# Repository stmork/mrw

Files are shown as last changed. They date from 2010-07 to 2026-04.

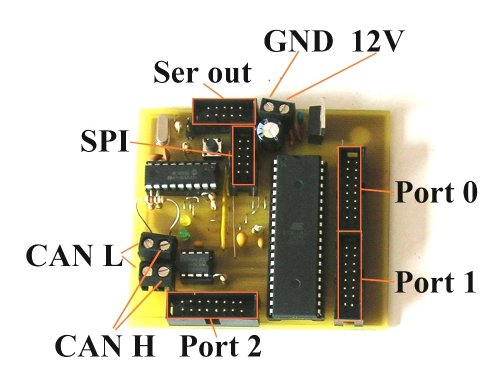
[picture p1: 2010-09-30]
Bilder/Trac/ControllerModul/AnschluesseMC.jpg

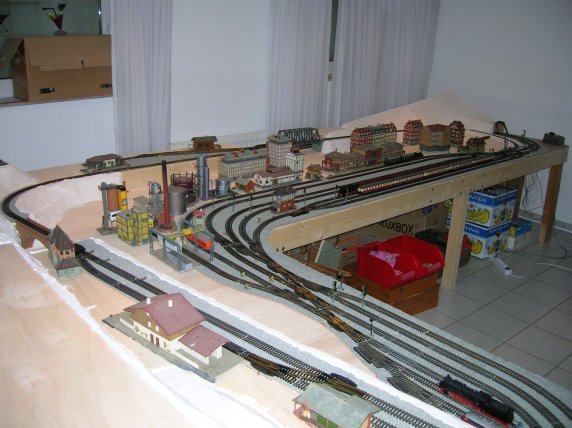
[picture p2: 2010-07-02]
Bilder/Trac/AnlageZwei/dscn4039.jpg

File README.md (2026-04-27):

# Modell(-bau-)basierte Eisenbahnsteuerung

Herzlich Willkommen auf den Informationsseiten der modell(-bau-)basierten
Eisenbahnsteuerung! Auf diesen Seiten wird die Entwicklung einer
eigenständig entwickelten Eisenbahnsteuerung dargestellt. Alle Ergebnisse
können auf diesen Seiten als Open Source (Eclipse Public Licence) eingesehen
werden. Schaut Euch den Quellcode an und nehmt Einblick in die
technischen Hintergründe des CAN-Bus und Microcontroller-Programmierung mit
dem ATmega32. Die ausführliche API bietet weiteres Hintergrundmaterial.
Schauen Sie sich auch die vielen
[Videos auf YouTube](https://www.youtube.com/playlist?list=PL6E0B186E9CC98026) an!

Viel Spaß!!

## Build- und Modellarchitektur

```mermaid
flowchart TB
subgraph Eclipse
 Modelrailway.umlclass -- converts --> Ecore --> GenModel
 GenModel --> Modelleditor-Plugin -- edit --> MRW.modelrailway
 Ecore --> Modelleditor-Plugin
 Ecore --> MRW-Generator --> MRW-Classes
 Xtext --> MRW-Generator
 MRW.modelrailway -- generates --> MRW-Classes -- compiles --> Control-Plugin
 end
 Control-Plugin -- deploys --> Application
 subgraph Eclipse-RPC-Application
 Application -. uses .-> Signal.properties
 Application -. uses .-> Gruppe.properties
 Application -. uses .-> Gleisteile.properties
 end

```

## MRW Firmware
Die Firmware ist in ein eigenes Repository migriert und wird hier nicht mehr
gepflegt.

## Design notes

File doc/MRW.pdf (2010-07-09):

## Modell(-bau-)getriebene Eisenbahnsteuerung

Motivation
Der Bau einer Modelleisenbahnanlage ist nicht nur technisch eine Herausforderung. Viele Kabel müssen über Kopf verlegt werden. Zum Teil ist die Topologie der Anlage so, dass viele Stellen relativ unzugänglich sind. Kann dort Verkabelung reduziert werden, vereinfacht das im erheblichen Maße die Installation. Aus diesem Grunde wurde die Steuerung so konzipiert, dass möglichst viel Verkabelungsaufwand gespart werden soll. Bei einer klassischen Anlage werden alle zu steuernden Bauteile mit dem Stellwerk verbunden. Eine simple Weiche hat drei Anschlüsse. Bei 30 Weichen sind das schon knapp hundert Kabel, die zum Teil über weite Strecken geführt werden müssen. Aus diesem Grund ist die Steuerung der Bauteile möglichst nah anzubringen. Es verbleibt nur noch die Stromversorgung und die Kommunikationsleitungen, die anlagenweit anzubringen sind. Die Steuermodule – im Folgenden CAN-
Knoten | genannt | - | sind | nicht
spezialisiert, das heißt, dass sie über ihre Mehrzweck-IO-Leitungen alle

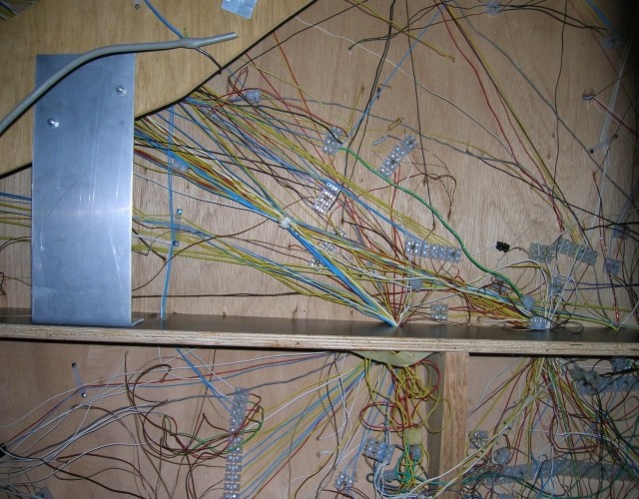
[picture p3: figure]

möglichen Erweiterungen ansteuern können. Die Gerätemodule haben keine Eigenintelligenz und dienen als Schnittstelle und Leistungsverstärker bzw. Schalter zwischen dem CAN-Knoten und dem Bauteil. Die Bauteile der Eisenbahnanlage werden direkt an die Gerätemodule angeschlossen und diese wiederum per Flachbandkabel an die Mehrzweckanschlüsse der CAN-Knoten. Jeder CAN-Knoten hat drei dieser Anschlüsse. Als zusätzliche Anschlussmöglichkeit hat jeder CAN-Knoten einen seriellen Anschluss, mit dem ein spezielles Lichtsignalmodul über ein 10-poliges Flachbandkabel angeschlossen werden kann. Die reine Verkabelung meiner eigenen Anlage mit 29 Weichen, 84 Gleisabschnitten, 45 Signalen gesteuert von 15 CAN-Knoten hat gerade mal fünf volle Tage gedauert.

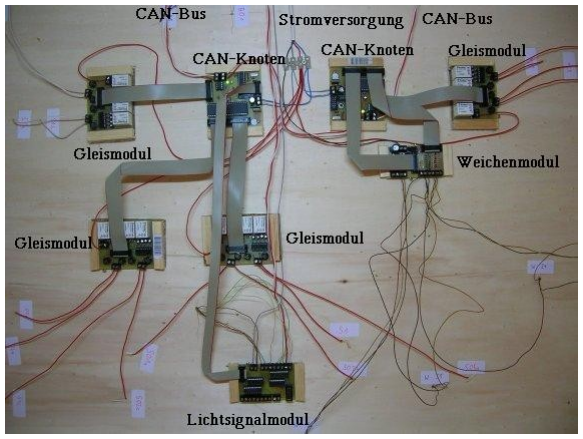
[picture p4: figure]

Als | Bussystem | wurde | CAN
gewählt. Ursprünglich von Bosch
entwickelt, wird es in fast jedem neueren Fahrzeug als Bussystem
verwendet. | Durch | die | raue
Umgebung im Automobil gilt der CAN-Bus als sehr robust und findet immer mehr Verwendung auch in anderen Bereichen, etwa in der
Automatisierungstechnik. | Auf
Grund | der | zwanzigjährigen
Geschichte ist | der CAN-Bus
ausgereift | und | kostengünstig
verfügbar. | Auf | die | in | der
Modellbahnwelt | benutzten
Protokolle wie z.B. DCC wurde bewusst verzichtet. Zum einen ist DCC nur eine Teillösung, weil eine Ansteuerung durch einen Rechner nicht in einer Spezifikation abgedeckt ist. Zum anderen ist die Möglichkeit der Rückmeldung begrenzt. DCC ist ursprünglich unidirektional ausgelegt. Die bidirektionale Nutzung liegt derzeit nur als Empfehlung vor. Des Weiteren haben sich andere Protokolle, die der Rückmeldung dienen etabliert. Insgesamt ist dadurch der Digitalmarkt im Modellbahnumfeld relativ unübersichtlich. Bei der Entwicklung der Steuerung ging es auch nicht darum, eine weitere Steuerung auf den Markt zu bringen und anderen Systemen Konkurrenz zum machen, sondern eine Machbarkeitsstudie für eine modellgetriebene Mikrocontroller-Firmware zu entwickeln. Aus diesem Grund wurde die Steuerung samt Rückmeldungsmöglichkeit als Ganzes völlig neu konzipiert. Zu berücksichtigen bleibt, dass die Steuerung nur den verbauten Anteil der Anlage, also Gleise, Weichen und Signale, ansteuern. Die Loks können unabhängig davon sowohl klassisch analog, als auch digital mit DCC angesteuert werden. Diese Steuerung nimmt keinen Einfluss auf das Verhalten von Lokomotiven!

Architektur
Grob gesehen besteht die Eisenbahnsteuerung aus einem Thick Client, der die Fahrstraßensteuerung und die Visualisierung über eine GUI übernimmt und der zu steuernden Hardware samt ihrer Mikrocontroller, welche die Ansteuerung der Geräte übernimmt. Die Schnittstelle zwischen einem High-Level-Rechner und der Eisenbahnanlage übernimmt die RS232-Schnittstelle.

Anlagenseitig ist direkt an der RS232-Schnittstelle ein CAN-Gateway angeschlossen. Dieses setzt die über RS232 laufenden Kommandos auf den CAN-Bus um. Am CAN-Bus sind in Reihe geschaltet die CAN-Knoten. Der CAN-Bus wird mit 128 KBit/s betrieben, was eine Länge von 500 Metern mit 110 CAN-Knoten möglich macht. Der CAN-Knoten kann Kommandos wie „Schalte Weiche 19 nach rechts“ oder „Schalte Signal P3 auf Hp1“ abarbeiten. Dabei hat dieser CAN-Knoten die vollständige Kontrolle über den Schaltvorgang. Als Rückmeldung kann dann Erfolg oder Fehler gemeldet werden. Des Weiteren können vom CAN-Knoten eigenständige Meldungen erzeugt werden. Das sind Gleisbesetztmeldungen, die durch fahrende Loks entstehen und manuelle Weichenschaltvorgänge.

Rechnerseitig wird ein Eclipse-RCP-Client verwendet. Dieser kommuniziert mit der RS232-Schnittstelle mittels der RXTX-Api. Die Modelleisenbahn wird in einem EMF-Modell beschrieben. Aus dieser Beschreibung wird zum Teil die GUI generiert. Mittels der GUI können Fahrstraßen ausgewählt und geschaltet werden. Dabei wird zwischen normalen Zugfahrten und Rangierfahrten unterschieden. Rangierfahrten können einen Bahnhof nicht verlassen. Die Berechnung einer Fahrstraße berücksichtigt belegte Gleisabschnitte sowie durch Fahrstraßen blockierte Gleisabschnitte. Die Schaltung einer Fahrstraße erfolgt in einer Abfolge von drei Kommandostapeln:

1. Schaltung der Weichen
2. Schaltung der Signale
3. Freigabe der Gleisabschnitte

Jeder Stapel muss vollständig und korrekt abgearbeitet werden, bevor der nächste Stapel bearbeitet wird. So kann verhindert werden, dass eine Weiche nicht in der korrekten Lage ist und so den Zug unter Umständen zur Entgleisung führt. Sobald alle Stapel bearbeitet sind, gilt die Fahrstraße als gesichert. Die von den CAN-Knoten erzeugten automatischen Rückmeldungen werden verwendet, um eine automatische Gleisfreigabe zu ermöglichen. Gleisabschnitte, die verlassen wurden, lassen sich so in neue Fahrstraßen einplanen. Manuelle Schalteingriffe von Weichen werden auch ausgewertet. Ist eine solche Weiche Bestandteil einer gültigen Fahrstraße, wird durch diesen Eingriff der Fahrweg verändert. Um dadurch bedingt Unfälle zu verhindern, wird die komplette

Fahrstraße aufgelöst.

Die Module

Die CAN-Module

Die Aufgaben des CAN-Gateway und der CAN-Knoten wurde schon beschrieben. Beide Module basieren auf Atmels ATmega32 Mikrocontroller. Sie haben 32 KByte Flash, 1 KByte EEPROM und 2 KByte SRAM. Des Weiteren verfügt der ATmega32 über 32 Mehrzweck-IO-Leitungen. Fünf Leitungen werden für die Kommunikation mit dem CAN-Controller MCP2515 über SPI-Interface verwendet. Der CAN-Knoten verbraucht weitere drei IO-Leitungen zur Kommunikation über das serielle Interface. Die restlichen 24 IO-Leitungen stehen für Steuermodule zur Verfügung.
Diese sind über drei Acht-Bit-Ports über 16-polige

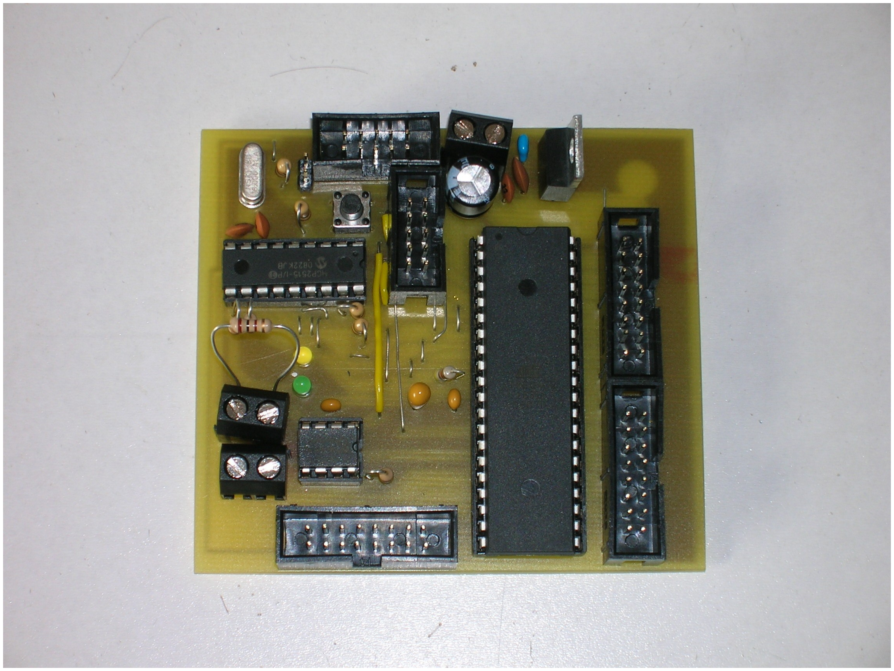
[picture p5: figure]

Flachbandstecker nach außen geführt. Über die restlichen acht Leitungen werden 5V, 12V und Masse als Stromversorgung an die externen Module geführt. Derzeit werden diese für simple Einund Ausgaben verwendet – es werden also nur Bits abgefragt bzw. Bits gesetzt. Ein Einsatz für die DA- und AD-Wandler stellt kein Problem dar, wird aber durch bisherige Module noch nicht verwendet. Das CAN-Gateway besitzt eine feste Firmware, die durch einen externen SPI-Stecker umprogrammiert werden kann. Die CAN-Knoten dagegen haben einen CAN-Bootloader. Über diesen kann neue Firmware über den CAN-Bus übertragen und auf dem Knoten selbst im System programmiert werden. Der Bootloader wird einmal initial über einen SPI-Anschluss geflasht. Für die Nutz-Firmware stehen so 28 KByte zur Verfügung. Der große Vorteil an diesem Verfahren ist, dass Firmwareupdates zentral in wenigen Sekunden auf alle Knoten gespielt werden können, ohne einen halben Nachmittag mit einem Programmiergerät unter der Anlage liegen zu müssen.

Das Gleismodul
Das Gleismodul kann vier Gleisabschnitte verwalten. Ein Gleisabschnitt kann über ein Relais stromlos geschaltet werden. Unabhängig vom Zustand des Relais kann festgestellt werden, ob auf diesem Gleisabschnitt ein „Stromverbraucher“ steht. Damit können Loks auf den Gleisen detektiert werden. Auch Waggons mit Beleuchtung lassen sich damit erkennen. Um die Anwesenheit von Waggons festzustellen, müssen die Achsen der Waggons mit einem Widerstand ausgestattet werden. Die Detektion erfolgt darüber, dass zwei antiparallel geschaltete Dioden bei Stromfluss
(beide | Polaritäten) | einen | Spannungsabfall

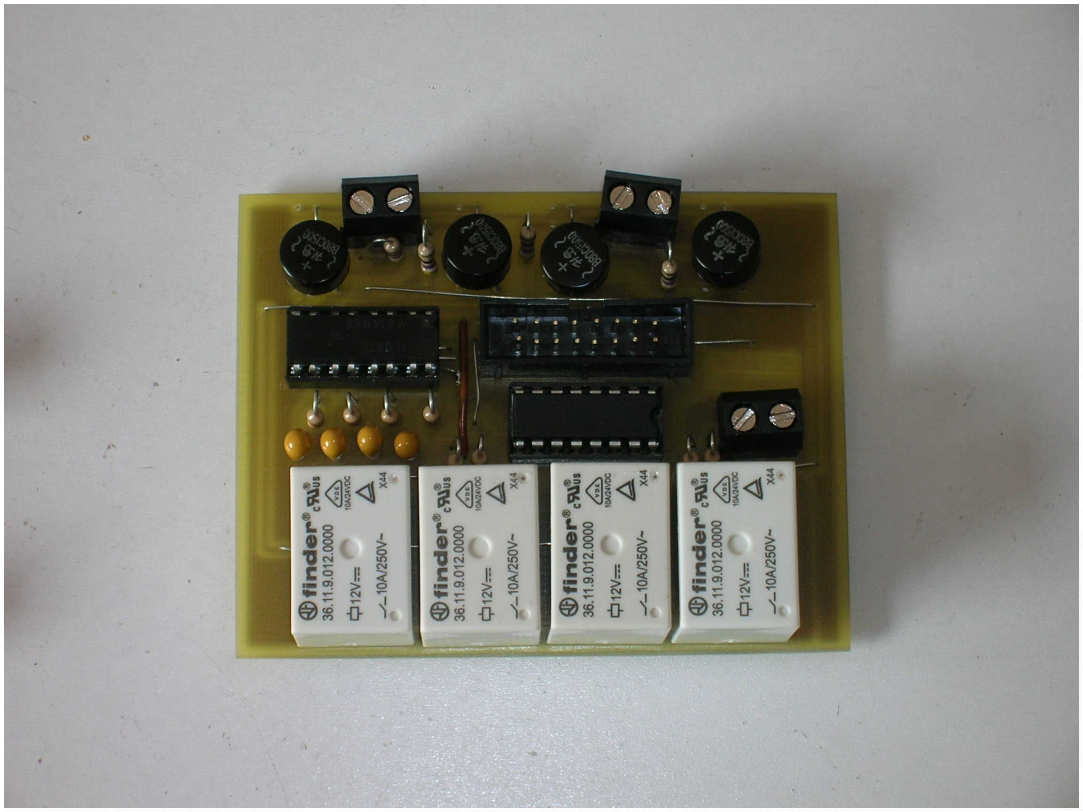
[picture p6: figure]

hervorrufen. Dieser steuert einen Optokoppler an und kann die Information somit an den CAN-Knoten weiterleiten. Da Fahrstrom über die Relais eingespeist werden muss, muss dieser auf das Gleismodul gelangen. Dieses geschieht über eine weitere Anschlussklemme.

Das Magnetartikelmodul

Das Magnetartikelmodul kann Weichen und Formsignale mit Spulenantrieb ansteuern. Haben Weichen eine Endabschaltung, lässt sich darüber auch die aktuelle Weichenlage feststellen. So kann einerseits ein Schaltvorgang beschleunigt werden, andererseits lassen sich dadurch auch manuelle Schaltvorgänge melden. Es können acht Spulen angesteuert werden, was vier Weichen entspricht. Die Weichenlage wird über acht weitere
Anschlüsse | gemeldet. | So | benötigt | das
Magnetartikelmodul zwei der CAN-Knoten-Ports.
Die Firmware der CAN-Knoten achtet darauf, dass
nur eine Weiche gleichzeitig geschaltet wird, um

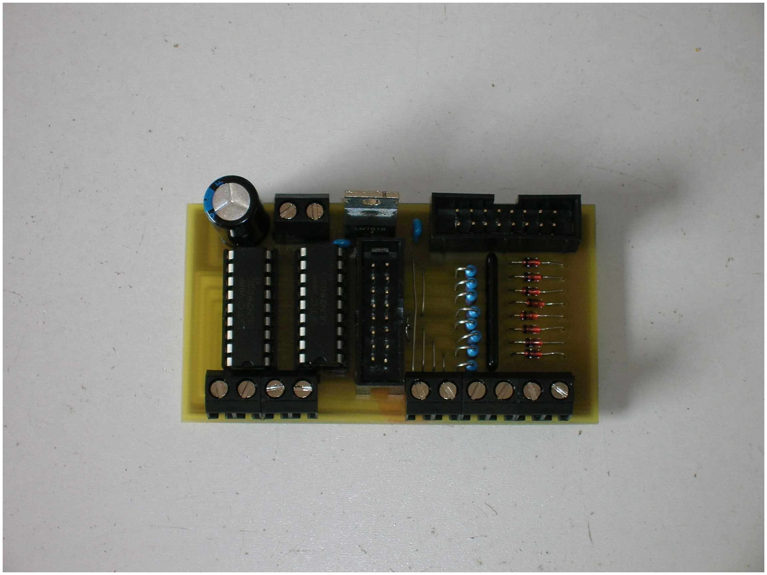
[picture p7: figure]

zu hohen Stromfluss zu vermeiden. Pro Spule sollte der Stromfluss nicht über 1A liegen. Die Weichen werden mit 18V geschaltet. Da diese Spannung nicht über das Flachbandkabel geliefert wird, muss es über eine zusätzliche Anschlussklemme bereitgestellt werden. Da auf dem Modul ein 18V-Spannungsregler vorhanden ist, kann das Modul mit 18V bis 50V versorgt werden, falls nicht 18V zur Verfügung stehen.

Das Lichtsignalmodul
Das Lichtsignalmodul steuert Lichtsignale an. Es wird über den seriellen Anschluss des CAN-Knotens angeschlossen. Die Lichtsignale können kaskadiert angeschlossen werden. Es werden jedoch nicht mehr als vier Module angesteuert. Jedes Modul hat 16 Anschlüsse. Diese können beliebig mit unterschiedlich großen Lichtsignalen gemischt
werden. | Ein | Ausfahrsignal | benötigt | fünf
Anschlüsse, ein Gleissperrsignal nur zwei. So lassen sich zwei Ausfahrsignale mit einem Vorsignal (vier Anschlüsse) und einem Gleissperrsignal mischen.
Der | CAN-Knoten | berechnet | zu | dieser
Anschlussbelegung abhängig vom anzuzeigenden

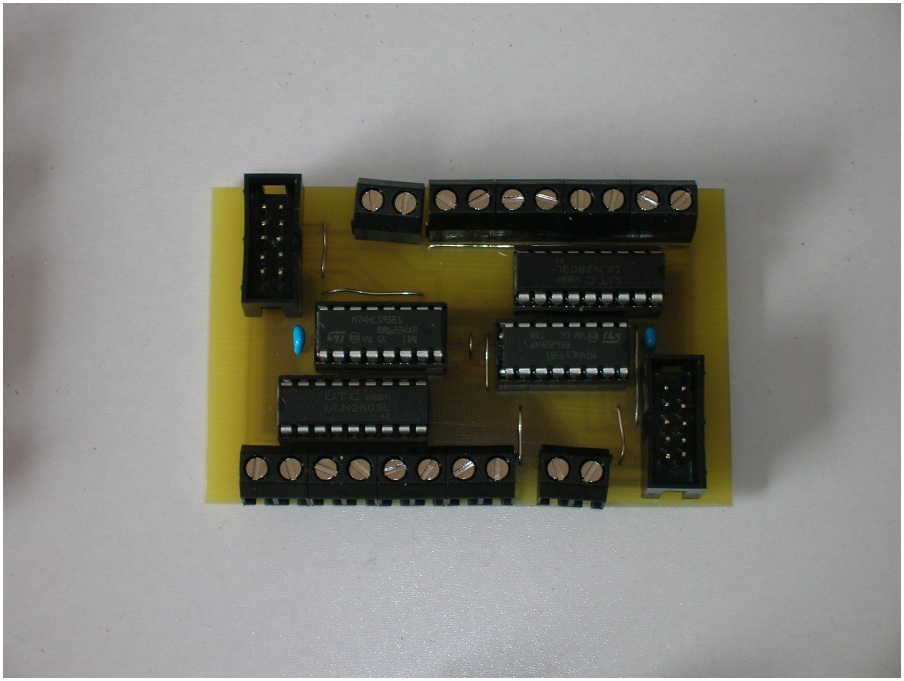
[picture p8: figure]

Signalbild ein Bitmuster, was seriell über die Anschlüsse an die simplen CMOS-Schieberegister weitergereicht wird. Über Leistungstreiber (ULN 2803) wird dann die Lämpchen bzw. LEDs des Signals angesteuert. Die Spannungsversorgung von 12V geschieht über Flachbandkabel vom CAN-Knoten.

Das Protokoll
Die Kommandos an die CAN-Knoten werden vom Rechner über RS232 auf den CAN-Bus geschickt. Dabei sind diese Kommandos schon in CAN-Frames eingebettet. Damit die Synchronisation der byteweisen Kommunikation zwischen Rechner und CAN-Gateway erhalten bleibt, wird die Übertragung mit einem Prüfsummen-Byte abgeschlossen. Die Aufträge lassen sich in drei Gruppen einteilen:
- Schaltaufträge
- Verwaltungsaufträge

- Konfigurationsaufträge

Die Struktur aller Aufträge ist gleich. Ein CAN-Telegramm kann zwischen keinem und acht Bytes beinhalten. Bei der Modellbahnsteuerung wird mindestens ein Byte transportiert: Das Kommandobyte. Je nach Kommando können weitere Bytes hinzukommen. Gerade die Konfigurationskommandos können die acht Bytes ausreizen.

Obwohl die ID eines CAN-Telegramms als Objektidentifier gemeint ist, wird bei der Modellbahnsteuerung damit der CAN-Knoten adressiert. Es können sowohl Standard Frames, als auch Extended Frames benutzt werden. Standard Frames werden für Controller-Aufgaben benutzt und Extended Frames zur Ansteuerung von Geräten. Die im Standard Frame benutzte ID adressiert somit den Controller und kann dadurch elf Bit breit sein. Alle IDs über 2000 und die „0“ sind reserviert. Die „0“ ist die Broadcast-Adresse, auf die alle CAN-Knoten hören. Des Weiteren hat das CAN-Gateway die Adresse 2047. Der restliche Raum zwischen 2000 und 2046 ist für Testzwecke reserviert. Obwohl die CAN-Knoten untereinander CAN-Messages austauschen könnten, wird bei der Modellbahnsteuerung davon derzeitig kein Gebrauch gemacht. Somit werden Kommandos nur vom CAN-Gateway verschickt. Die Antworten der CAN-Knoten laufen immer zum CAN-Gateway zurück.

Werden Schaltaufträge an Geräte gesendet, wird immer ein Extended Frame verwendet. Von den zusätzlichen 18 Bit werden „nur“ 16 verwendet und wird als Gerätenummer bezeichnet. Die restlichen Bits stehen auf 0. Somit könnten theoretisch 65536 Geräte pro CAN-Knoten angesteuert werden. Da die Konfiguration im EEPROM des CAN-Knotens hinterlegt wird, ist die Zahl der Geräte auf die Größe des EEPROMS begrenzt. Beim ATmega32 sind das ein Kbyte. Somit kann ein ATmega32 maximal 64 Geräte verwalten.

Die Antworten haben als Zieladresse immer das CAN-Gateway und liegen grundsätzlich als Extended Frame vor. Die Standard-ID ist dann immer 2047 für das Gateway und die zusätzlichen 18 Bit der Extended-ID umfassen die absendende Controller-ID. Dadurch ist eine saubere Arbitrierung des CAN-Busses möglich, wenn z.B. auf ein Broadcast-Ping alle CAN-Knoten antworten müssen. Die Antworten enthalten neben dem ausgelösten Kommando noch einen ein Byte großen Antwortcode. Zusätzlich werden vier Bytes für die Absende-ID (also Controller-ID und Gerätenummer) benötigt. Die restlichen zwei Bytes können für zusätzliche Informationen benutzt werden. Hier können Weichenlage, Gleisbesetztmeldung sowie Statusinformationen über den Mikrocontroller untergebracht werden. Ein Kommando muss nicht zwingend zu einer Antwort führen. Es kann auch sein, dass ein Kommando sogar zeitversetzt mehrere Antworten auslöst. Ein Weichenschaltauftrag meldet zuerst, dass der Auftrag eingereiht wurde. Nach erfolgreicher Ausführung wird einerseits der Erfolg gemeldet, aber auch zusätzlich die erreichte Endlage. So können auf höherer Ebene die Endlagenmeldungen unabhängig von den Schaltaufträgen verarbeitet werden.

Die Stellwerks-Software
Die Stellwerks-Software ist zum Teil aus modellgetrieben generiert. Die Hauptlogik ist aber klassisch implementiert. Die GUI basiert auf Eclipse RCP/SWT. Mit ihr werden Fahrstraßen ausgewählt und der Schaltvorgang ausgelöst. Dabei wird intensiv von Multi-Threading Gebrauch gemacht. Dies wird durch das asynchrone Auftreten von Rückmeldungen nötig. Sämtliche Zustände werden sofort ausgewertet und visualisiert. Es kann sogar parallel ein automatischer Modus aktiviert werden, der aus einem Schattenbahnhof zufällig Züge auswählt und diese durch wieder zufällig ausgewählte Gleise eines Bahnhofs fahren lässt. Die Visualisierung der GUI zeigt an, ob eine Fahrstraße geschaltet wird (gelb) oder fertig geschaltet ist (grün). Besetzte Gleisabschnitte werden orange angezeigt. Auch der Schaltzustand der Signale wird dargestellt. Befindet sich noch ein anhängiger Weichenschaltauftrag, wird die Weichennummer blinkend dargestellt. Des Weiteren befinden sich im Gleisbild Checkboxen, die zur Planung einer Fahrstraße herangezogen werden.

Während die GUI recht übersichtlich erscheint und nur wenig Eingriffsmöglichkeiten zu bieten scheint, sind in der zu Grunde liegenden Logik viele komplexe Vorgänge implementiert. Als erstes sei die Berechnung einer Fahrstraße aus selektierten Gleisabschnitten erwähnt. Dieses Verhalten entspricht dem Vorbild, bei dem durch Start- und Zielwahl ebenfalls eine Fahrstraße gebildet werden kann. Die Fahrstraßenberechnung berücksichtigt schon belegte Gleisabschnitte sowie durch andere Fahrstraßen verplante Gleisabschnitte. Im Modell sind an einer Weiche bevorzugte Abzweigungen modelliert. Diese werden bei der Fahrstraßenwahl zu erst gewählt. Erst, wenn ein Abzweig nicht zum Ziel führt, wird der andere Abzweig gewählt. Die Modellierung gibt auch Abzweigungen („Kurven“) an. Dadurch können Langsamfahrstellen forciert werden, die sich im Signalbild niederschlagen. Alle Signalbilder werden korrekt berechnet. Dies bezieht sich auf Langsamfahrstellen, Vorsignale, mit Hauptsignalen kombinierte Vorsignale sowie durch Rangierfahrten bedingt die Gleissperrsignale insbesondere in Verbindung mit Ausfahrsignalen.

Automatische | Rückmeldungen
der | CAN-Knoten | werden
ebenfalls ausgewertet. Dies ist besonders für die automatische Gleisfreigabe nötig. Verlässt eine Lok einen Gleisabschnitt und
befindet | sich | im | darauf
folgenden, dann kann dieser
Gleisabschnitt | stromlos
geschaltet werden und für eine neue Fahrstraßenplanung zur
Verfügung | | stehen. | Die
Bedingung, dass der darauf folgende Abschnitt belegt ist, ist

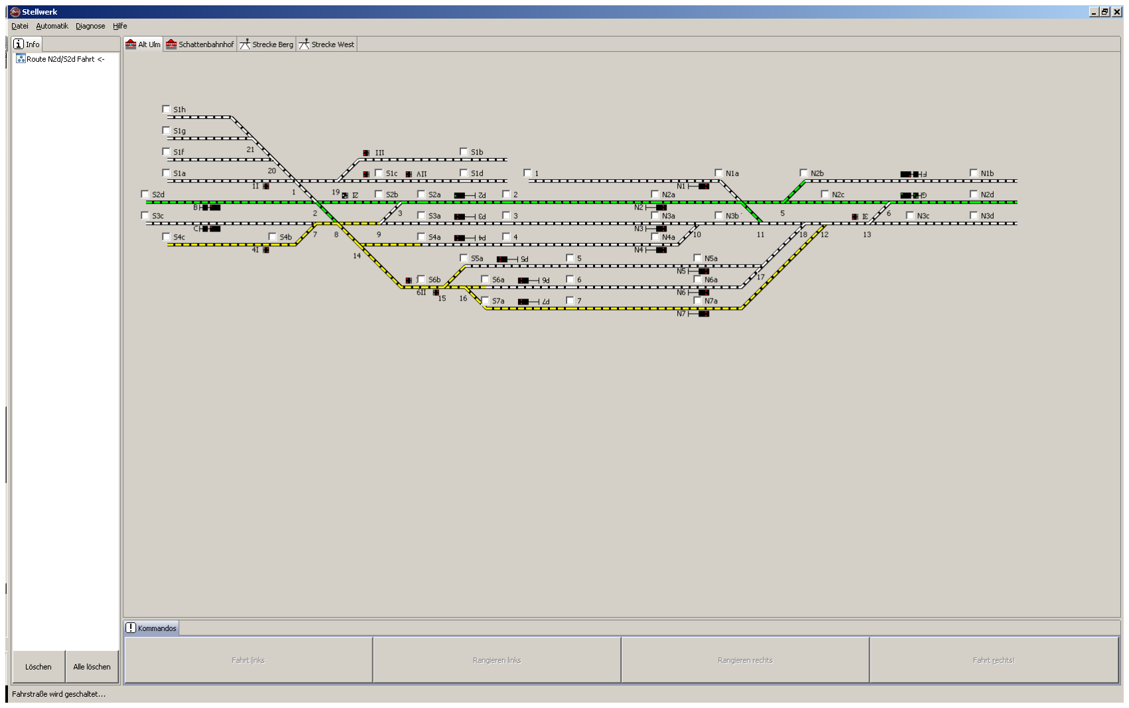
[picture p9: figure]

an dieser Stelle wichtig. Gerade beim Zweileiter-Gleichstrombetrieb einer Modelleisenbahnanlage kann es zu Kontaktschwierigkeiten durch Dreck kommen. In diesem Falle verschwindet die Lok scheinbar von den Gleisen. Das darf aber nicht zu einer Gleisfreigabe führen. Hat ein Zug den Zielabschnitt erreicht, wird die Fahrstraße komplett aufgelöst. Dadurch ist kein Benutzereingriff mehr nötig.

Das Metamodell
Das | Metamodell | beschreibt, | wie | allgemein | eine
Modelleisenbahnanlage aussehen kann. Es beinhaltet den gesamten Gleisplan, die Aufteilung der Gleisabschnitte sowie die Gruppierung in Bahnhöfe und Strecken. Des Weiteren sind unterschiedliche Signale im Modell enthalten. Weitere Eigenschaften wie bevorzugte Abzweigungen und Abzweigungen (im Sinne von „Kurven“) ergänzen die Modellbeschreibung. Das Metamodell ist als EMF-
Modell | mit | MagicDraw | erstellt | worden. | Durch | die
openArchitectureWare-Cartridge „uml2ecore“ kann das in ein ECore umgewandelt werden. Aus diesem ECore kann für Eclipse ein Editor erstellt werden, mit dem eine Eisenbahnanlage erfasst werden kann. Jedem Gleisteil kann eine Zählrichtung vorgegeben werden, sodass Fahrtrichtungen bei der Fahrstraßenschaltung berücksichtigt werden können. Die Validierung hat unter Anderem die Aufgabe zu prüfen, ob die modellierte Zählrichtung für alle Gleisteile schlüssig ist. Aus diesem Modell werden Code-Teile generiert, die eine Konfiguration
der | Eisenbahn | enthält. | Daraus | wiederum | können | die
Konfigurationskommandos erzeugt werden, die die CAN-Knoten mit den Geräteinformationen versorgt. Des Weiteren wird diese Konfigurationsinformationen für die Anzeige der GUI benötigt.

Modellgetriebene Firmware

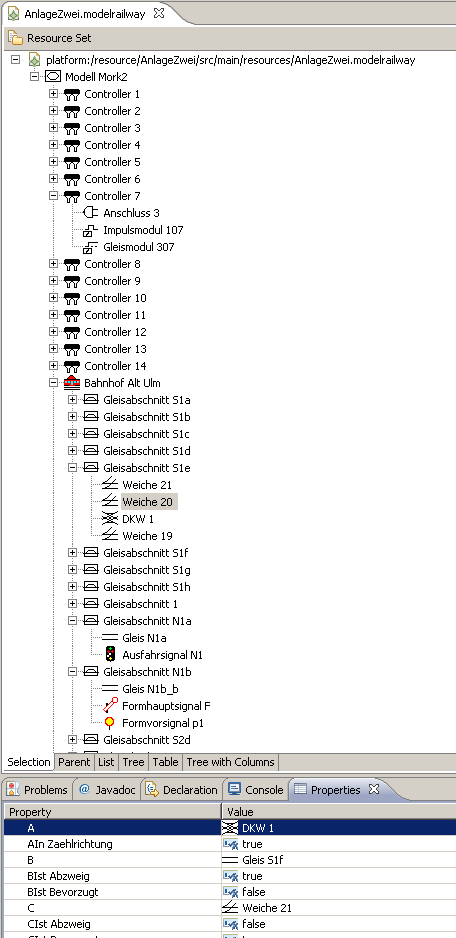
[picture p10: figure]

In der ersten Fassung war die Firmware der CAN-Knoten als Referenzimplementierung noch klassisch implementiert. Die Kommandoverarbeitung in der Firmware der CAN-Knoten war ein unschönes Stück Spaghetti-Code. Aus diesem Grund wurde ein Zustandsdiagramm gefertigt, das die Betriebszustände des CAN-Knoten enthält. Die

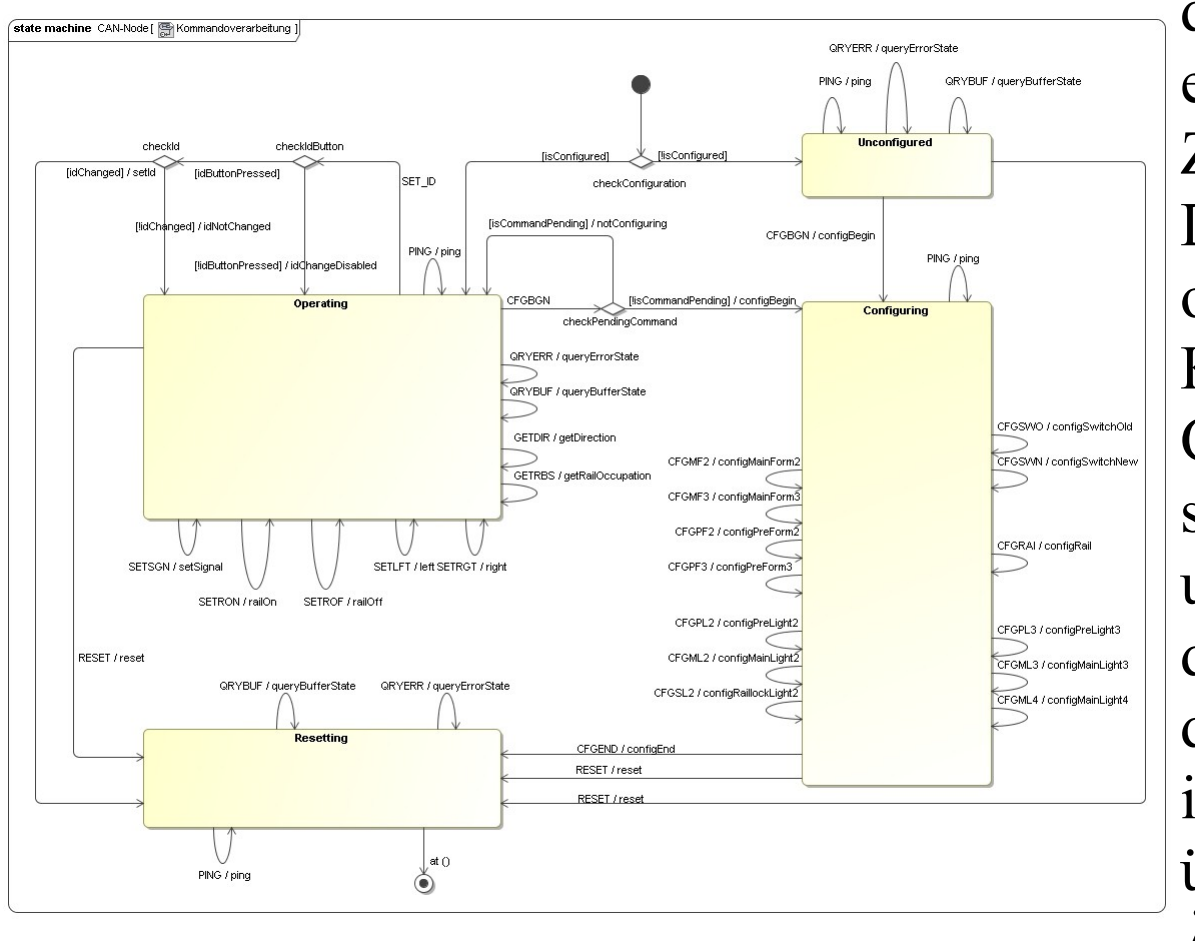
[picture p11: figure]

eingehenden | Kommandos | sind | als
Zustandsübergänge | modelliert. | Aus | diesem
Diagramm | wird | mit | Hilfe | von
openArchitectureWare | der | Code | für | die
Kommandoauswertung generiert. Der generierte Code enthält zwar relativ viele Callbacks und switch/case-Anweisungen und bläht den Binärcode um ca. 1,5 KByte auf. Das stellt aber kein Problem dar, weil jetzt noch Platz für ca. 18 KByte im Flash des ATmega32 vorhanden ist. Ein weiterer Vorteil ist, dass der generierte Code wesentlich übersichtlicher aussieht und somit wartbarer wird.
Änderungen | und | Erweiterungen | der
Steuerkommandos lassen sich jetzt viel leichter einpflegen. Die Integration des generierten Codes in den bestehenden Firmware-Rahmen gestaltete sich als unproblematisch, da der restliche klassisch implementierte Teil nur aus Service-Methoden zur Ansteuerung der Hardware dient.

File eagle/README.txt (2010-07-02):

Hinweise zur Platinenbestellung

- Alle Platinen sind einseitig. Top-Layer sind Loetbruecken. 
  Viele Loetbruecken ueberlappen oder kreuzen sich. Kein Problem. 

- Kein Loetstopplack, kein Bestueckungsdruck (falls Aufpreispflichtig)

- Die Durchmesser der Bohrloecher koennen auf die vorhandenen 
  Standard-Bohrerdurchmesser aufgerundet werden.  Exakter Durchmesser nicht wichtig.

- Die grosse Bohrung fuer Spannungsregler 7805 / 7818 (Metallflaeche fuer Kuehlung) 
 sind nicht notwendig. Regler / Kuehler werden nicht festgeschraubt.

- Manche Bauteile ragen aus der Platinenbegrenzung heraus. Dies ist kein Problem.

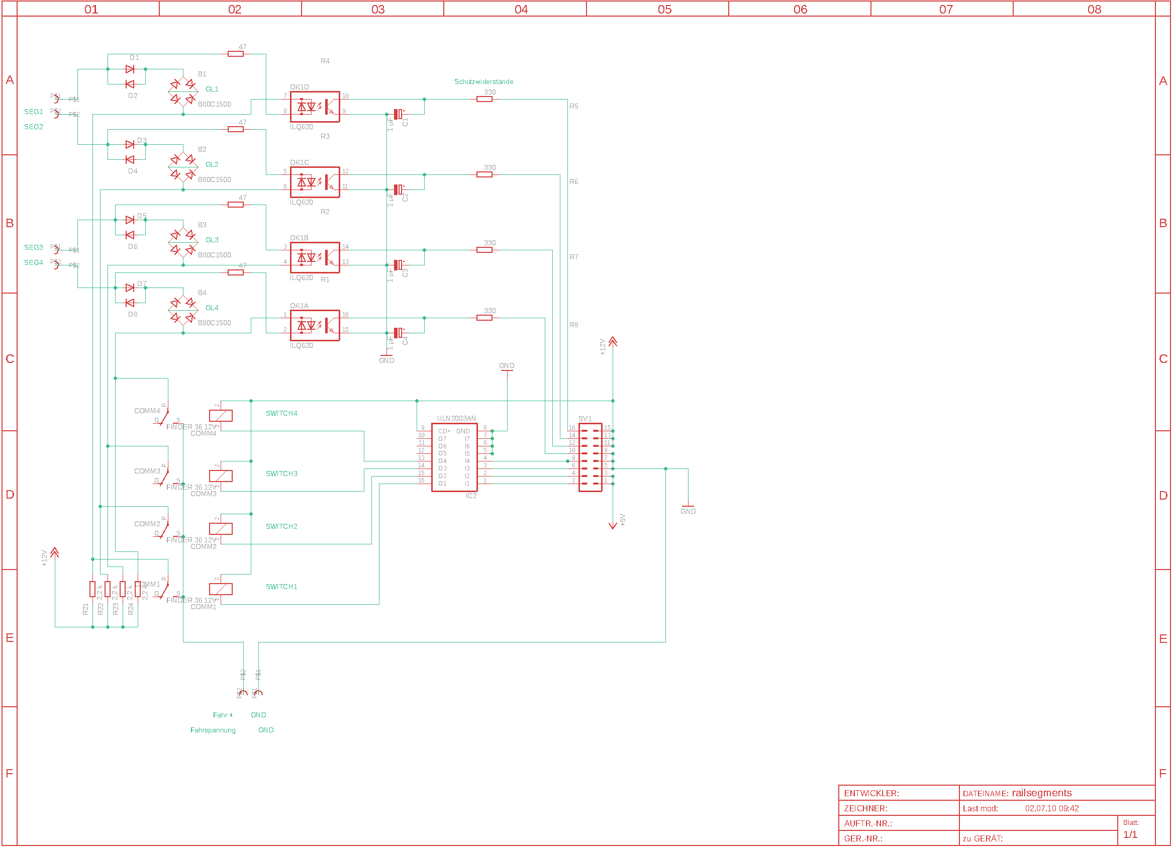
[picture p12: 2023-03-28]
eagle/images/SectionModule.png

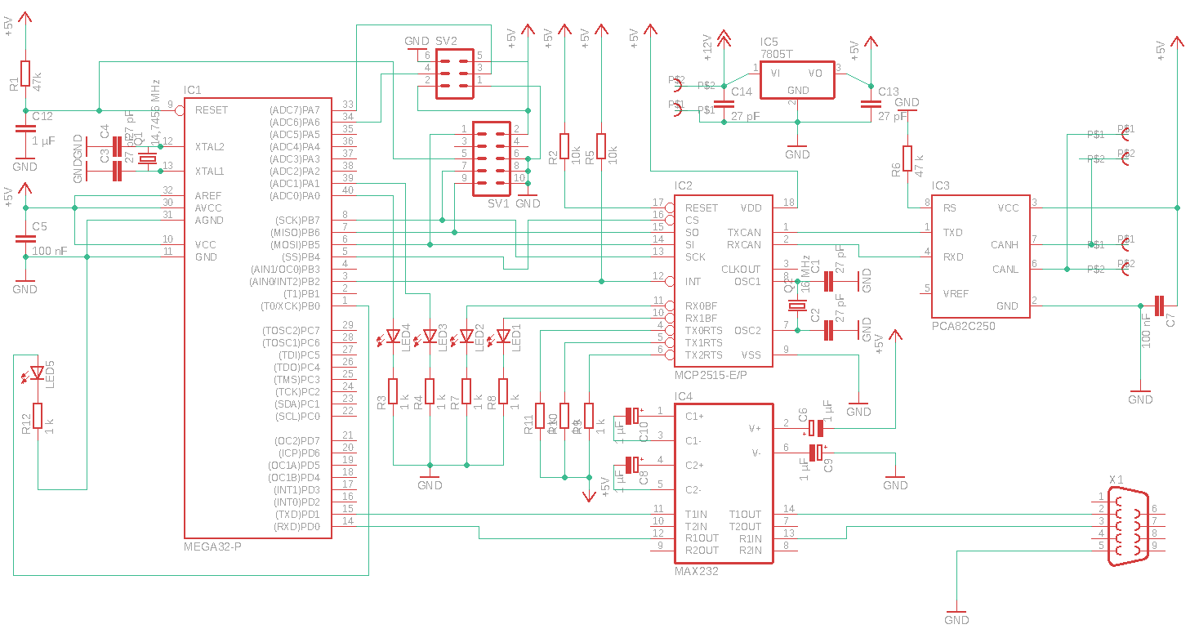
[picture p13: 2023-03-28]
eagle/images/CAN-Gateway.png

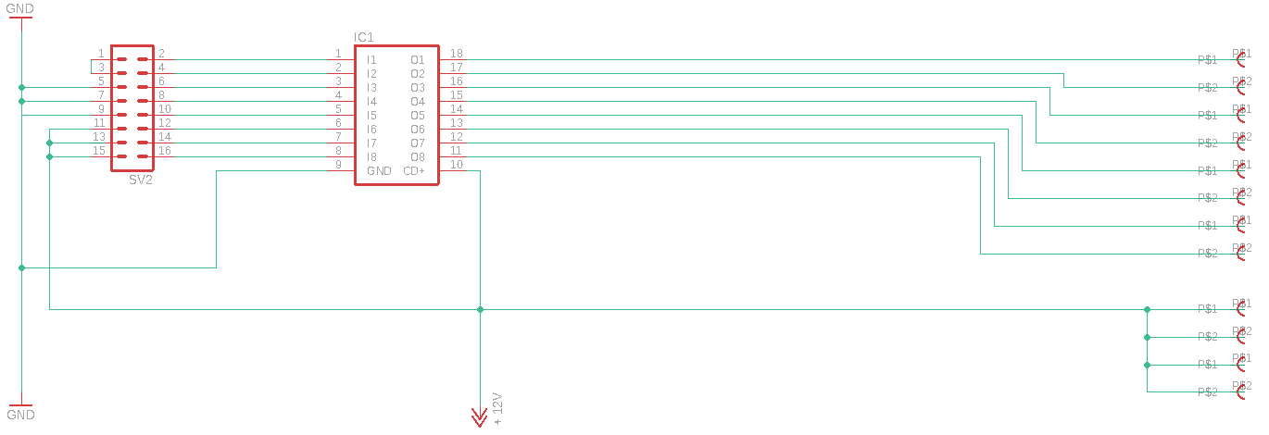
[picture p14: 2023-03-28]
eagle/images/LightModule.png

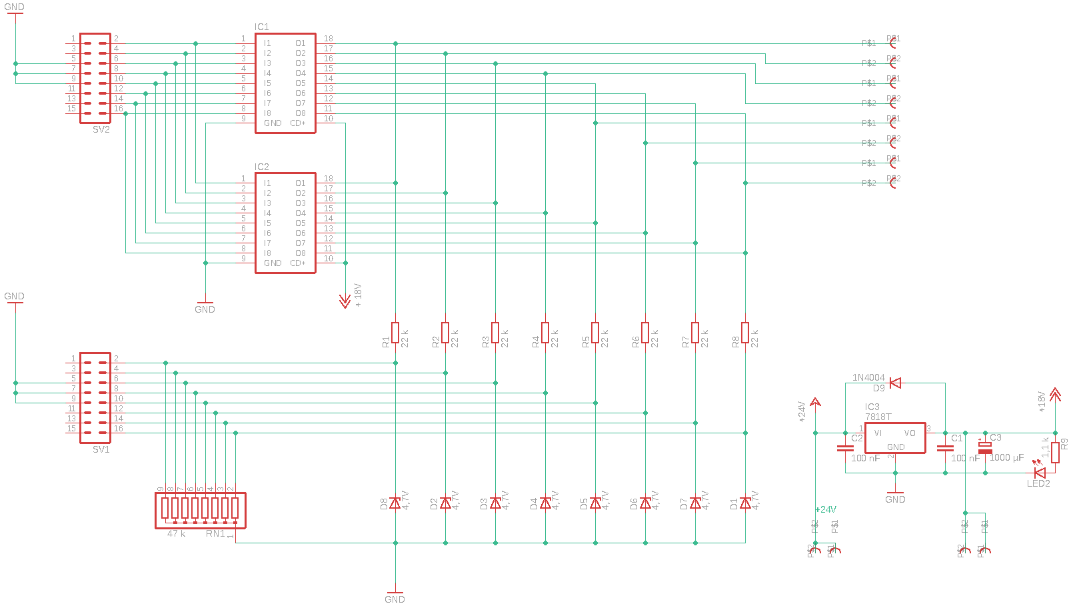
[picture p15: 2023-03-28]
eagle/images/SwitchModule.png

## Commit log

2010-07-02 * Erster Import
    [gateway.sch, gbm.sch, mc.brd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]
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2010-07-15 * Diagramm verschoenert. * Quelle der Layout-Informationen ausgegeben.
2010-09-02 * Studien am Buffer Overflow durchgeführt. * Überlauf wird mit LED quittiert. * Das Versenden der CAN-Meldungen vermeidet Überlauf.
2010-09-11 * Das Setzen der ID ist jetzt auch im UNCONFIGURED Modus möglich.
2010-09-11 * Hui! Die OIDs von Broadcast und Gateway wurden ausgetauscht. Somit haben Antworten höhere Priorität als Broadcasts. Das erforderte ein Umprogrammieren der Bootloader. Diese sind jetzt auf neuestem 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
2010-09-11 * Kommandoverarbeitung aktualisiert. Es kann jetzt auch im unkonfigurierten Modus die ID gesetzt werden.
2010-09-11 * Einige Kommandos geben jetzt Ergebnisse in vier Bytes zurück. Dadurch wird nur eine statt drei Ergebis-Meldungen erzeugt.
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2010-09-17 * Hardware-mäßige Pulsweitenmodulation (PWM) ist vollkommen überbewertet ;-)
2010-09-18 * Soft-PWM nur über Timer: o Timer1 steuert die PWM o Timer2 ermittelt die Helligkeit
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2010-09-20 * EnumTest repariert. * PWM auf mrw_config umgestellt.
2010-09-21 * PWM für Lampen in eigentliche Firmware integriert.
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2010-09-21 * Neues Kommando eingeführt: SENSOR. * Helligkeitswerte werden zum Schalten der Lampen herangezogen.
2010-09-22 * Die Gerätekonfiguration wird sortiert gespeichert. Das beschleunigt die Suche.
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2010-09-22 * Lampen in Modell-Klasse eingebaut und entsprechend den Generator angepasst.
2010-09-26 * Beleuchtungsmodul fertiggestellt.
    [light.brd, light.sch]
2010-09-26 * Metamodell eingedeutscht und Mehrzahl angepasst. * Lichtmodul editiert. * Weitere Profile hinzugefügt.
    [light.brd]
2010-09-27 * Metamodell korrigiert und Generator entsprechend angepasst.
2010-09-27 * Dokumentation der Kommandos aufbereitet. * Leuchtmittel werden statistisch im Generatorlauf ausgegeben.
2010-09-30 * Profile werden jetzt konfigurierbar. Es gibt auch Zufallsprofile für Neonlampen und Gaslampen. * Dementsprechend wurden Zufallszahlen eingeführt.
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2010-10-01 * Gateway editiert.
    [gateway.brd, gateway.sch]
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2010-10-02 * Weitere Pufferung - keine Flutung von Sensorwerten mehr.
2010-10-06 * Statistik für Lampen im Generator ergänzt. * Schwellwert der Lampen bei Anlage 2 abgesenkt. * Hysterese bei Lampenschaltung eingebaut. * Erste Sensorwerte kommen fünf Sekunden nach Booten. * Refact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
2010-10-09 * Hysterese besser implementiert. * Bei ausgeschaltetem Licht wird Rechenzeit gespart, indem das Licht einfach nur ausgemacht wird und nicht gedimmt.
2010-10-11 * Reset-Handling verbessert. * Zwei neue Laternen und eine Telefonzelle konfiguriert.
2010-10-17 * Verbindung wird resynchronisiert, wenn ein Prüfsummenfehler auftaucht. * Neuer CAn-Knoten 16 montiert. * Gleisabschnitte ummontiert. * Weitere Lampen montiert.
2010-10-19 * Ich weiß nicht, warum bei jedem Leseversuch über RS232 ein Puffer allokiert wird. Jedenfalls kann das die Ursache dafür sein, dass ChecksumExceptions auftreten wenn just durch die Allokation eine G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
2010-10-20 * Message Queuing umgestellt. Das Reinreichen wartet nicht mehr auf Ausführung auf der Gegenseite. Dafür ist das Lesen und Schreiben über RS232 exklusiv-oder. * Die Gültigkeit der MrwMessages wurde i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
2010-10-24 * Dämon programmiert, der RS232 an TCP proxifiziert. Dabei zeigt sich dieselbe Problematik wie beim direkten Zugriff auf RS232: Es gehen Bytes verloren. Vermutlich ist der Steuerrechner mit nur einem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
2010-11-01 * Zahl der konfigurierten Geräte wird überprüft. * Einfaches Licht wird direkt in seriellen Puffer übertragen. * Controller mit ID 11 simuliert - kein Problem ?!? * int in uint8_t übertragen.
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2010-11-04 * Bug im Bootlader gefixed: SENSOR-Werte sorgen nicht mehr für Verlassen der Bootschleife vor erstem FLASH_DATA-Kommando. * Bessere Zeigerarithmethik.
2010-11-06 * Gateway-Layout.
    [gateway.brd, gateway.sch]
2010-11-06 * Board ein wenig kleiner gemacht.
    [light.brd]
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2010-11-08 * Neues Layout
    [light.brd, light.sch, switch.brd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]
2010-11-10 * Gateway hängt kein 0x68 mehr an. * CAN-Dumps haben jetzt auch Ausgabe der Millisekunden. * Weitere Änderungen an Board-Layouts. * Timeout-Handling im MrwController verbessert.
    [gateway.brd, gateway.sch, mc.brd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]
2010-11-10 * Gateway weiterentwickelt.
    [gateway.brd, gateway.sch]
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2010-11-11 * AT90CAN-Board angefangen.
    [atcan.brd, atcan.sch]
2010-11-12 * Board-Design erweitert. * Richtige Prüfung auf Verfügbarkeit der seriellen Schnittstelle.
    [atcan.brd, mc.brd]
2010-11-12 * Ich krieg' Kopfschmerzen.
    [atcan.brd, atcan.sch]
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2010-11-13 * Restliche Bauteile in SMD umgewandelt.
    [atcan.brd, atcan.sch, light.brd]
2010-11-13 * So! AT90CAN128 ist fertig.
    [atcan.brd, atcan.sch]
2010-11-17 * Bauteile von 1206 auf 0603 geändert. * Abblockkondensator ergänzt.
    [atcan.brd, atcan.sch, mc.brd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]
2010-11-17 * Gateway als SMD angefangen.
    [atcan.brd, atcan.sch, gateway.brd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]
2010-11-19 * Weichenmodul als SMD gebaut.
    [switch.brd, switch.sch]
2010-11-19 * Kleine Layout-Verbesserung.
    [switch.brd]
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2010-11-25 * Kleiner gemacht.
    [gateway.brd]
2010-11-28 * Ringpuffer effizienter genutzt. * Meldung wird erst aus Empfangspuffer entfernt, wenn diese verarbeitet wurde.
2010-11-30 * Firmware optimiert: o weniger Aktualisierungen auf dem seriellen Anschluss. o voll gedimmtes Licht braucht keine Rechenzeit mehr. * Jede gedimmte Lampe wird mit Verzögerung eingeschaltet. Da das in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
2010-12-02 * Platinengröße korrigiert.
    [mc.brd]
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2013-02-06 * Von Emma auf JaCoCo umgestiegen, um für das JDK 7 kompatibel zu bleiben. * Findbugs aktualisiert und neue Warnungen beseitigt.
2013-05-14 * Logging so angepasst, dass Start und Stop im Log erkennbar sind.
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2014-01-02 * HTML der Update Site korrigiert.
2015-03-03 * Umwandlung des Quellcodes in UTF-8. * Subversion-Probleme beseitigt.
2016-06-26 * Findbugs erneuert und Filter für Tests ergänzt. * JaCoCo erneuert. * MRW ist jetzt mit JDK 8 lauffähig.
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
